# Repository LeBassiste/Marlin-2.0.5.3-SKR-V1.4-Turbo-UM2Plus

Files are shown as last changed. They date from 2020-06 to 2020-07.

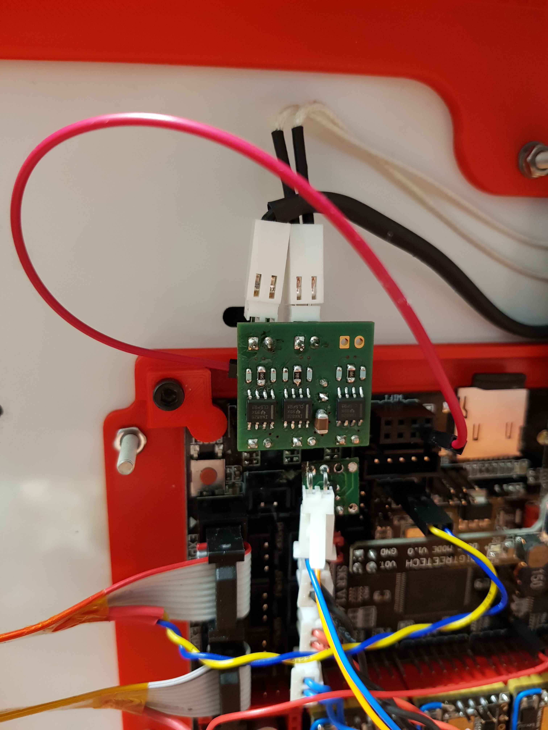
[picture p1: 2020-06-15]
PT100_Amp_Close-up.jpg

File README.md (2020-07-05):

# Marlin-2.0.5.3-SKR-V1.4-Turbo-UM2Plus
Marlin 2.0.5.3 Settings for BIGTREE SKR 1.4_Turbo, TMC5160 to drive Ultimaker UM2+ 3D Printer
version V2 contains updated and sanitized header files to reflect changes in
configuration.h
configuration_adv.h
pins_BT_SKR_c ommon.h
search for "habe" to find all modifications

reduced spill when preloading hotend before print.
increased motor currents to 800 mA and 32 microsteps to improve wall smoothness.

1.Required Hardware					
  a.  1	 BTT SKR 1.4 Turbo				
  b.  4	TMC5160 Stepper drivers				
  c.  1	BTT DCDC Power Module for SKR 1.4				
  d.  1	 PT100 Pre-Amplifier (Ultimaker Style), 3 channel, must use VDD = 3.3 VDC (DIY), see KICAD file	SKR14_PT100_Amp		
  e.  1	MOSFET Adapter Board to run Hotend Fan off of SERVO connector (DIY), see KICAD file SKR14_FAN_DRIVE				

2. What will these Mods do?					
	a.  Enable flicker-free dimmable Case Lighting, using the original Ultimaker Case LEDs @ 24 VDC and high frequency PWM dimming		
	b.  enable PWM-controlled Parts Fan				
	c.  enable PWM-controlled 5VDC for use with Hotend Fan	(needs extra MOSFET and Diode, driven from SERVO connector)			
	d.  increase Bed-Heater and Hotend-Heater PWM to 60 Hz to smoothen power consumption (note: you must use PID for Bed Heater). 
      This improves print quality!				
	e.  enable ulticontroller display and Clickwheel+LEDs as published by Anthrix https://community.ultimaker.com/topic/30786-ultimaker-with-skr-14/

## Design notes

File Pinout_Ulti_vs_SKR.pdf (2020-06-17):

Marlin 2.0.5.3 Settings for BIGTREE SKR 1.4_Turbo, TMC5160 to drive Ultimaker UM2+ 3D Printer

Required Hardware | | this sheet version: | 0.2 | added info about removing R25, R26
1 BTT SKR 1.4 Turbo
4 TMC5160 Stepper drivers
1 BTT DCDC Power Module for SKR 1.4
1 PT100 Pre-Amplifier (Ultimaker Style), 3 channel, must use VDD = 3.3 VDC (DIY)
1 MOSFET Adapter Board to run Hotend Fan off of SERVO connector (DIY)
What will these Mods do?
| Enable flicker-free dimmable Case Lighting, using the original Ultimaker Case LED-Strips
| enable PWM-controlled Parts Fan
| enable PWM-controlled 5VDC for use with Hotend Fan
| increase Bed-Heater and Hotend-Heater PWM to 60 Hz to smoothen power consumption (note: you must use PID for Bed Heater). This improves print quality.
| enable ulticontroller display and Clickwheel+LEDs (as published by Anthrix here:…) | https://community.ultimaker.com/topic/30786-ultimaker-with-skr-14/
Item | Spec1 | Spec2 | Spec3 | Ultimainboard | SKR 1.4 Port | SKR 1.4 | SKR-Spec1 | !!! Required HW Changes !!! | where?
Bed-Heater | 24VDC | SW-PWM | Screw Term | J21:1-2 / Heated-Bed | P_205 | HB | | | File | line
Bed-Temp | PT100 | MOLEX 2 | J13 / Temp3 | P_025 | TB | JJ12

must use Ultimaker-Style PT100 Pre-Amp
| | | | | | | must remove R26 on SKR board | configuration.h | 415 | #define TEMP_SENSOR_BED 20
Case Light | 24VDC | HF-PWM | MOLEX 2 | J15 | P_203 | FAN0 | Configuration_adv-h | 431 | #define CASE_LIGHT_PIN P2_03
E-Stepper | | | J30 | | E0M
Hotend-Fan | 5VDC | PWM | J34 | P_200 | SERVOS | J22:1_SIG, :2_NPWR, :3_GND | must use BTT DC/DC Extender and extra MOSFET | Configuration_adv-h | 423 | #define E0_AUTO_FAN_PIN P2_00
Hotend-Heater | 24VDC | SW-PWM | J21:5-6 / Heater 1 | P_207 | HE0
Hotend-Temp | PT100 | MOLEX 2 | J7 | P_024 | TH0 | J11
Part Fan | 24VDC | PWM | J14 | P_204 | HE1 | must use Ultimaker-Style PT100 Pre-Amp must remove R25 on SKR board | configuration.h | 409 | #define TEMP_SENSOR_0 20
| | | | | | | pins_BTT_SKR_common.h | 66 | #define FAN1_PIN P2_04
| | | | | | | | 86 | #define FAN_PIN P2_04
X-Stepper | J27
X-Stop | | J5 | P_129 | X-Stop | J1:1_P5, :2_GND, :3_SIG | connect to :2_GND, :3_SIG, pull to GND on activate
Y-Stepper | | J28
Y-Stop | | J8 | P_128 | Y-Stop | J3 | connect to :2_GND, :3_SIG, pull to GND on activate
Z-Stepper | | J29
Z-Stop | | J6 | P_127 | Z-Stop | J4 | connect to :2_GND, :3_SIG, pull to GND on activate
Ulticontroller E1 | 2Mx5_0.100 | J32 | | E1DET | | Anthrix mod (I2C and 3.3V supply) | configuration.h | 1933 | #define ULTI_CONTROLLER
Ulticontroller E2 | 2Mx5_0.101 | J33 | | E0DET | | Anthrix mod (I2C and 3.3V supply)
PWM frequency for Case Light, Fans_1 | P_124 uses 60 Hz PWM, not useful for lighting | HW-PWM frequeny default is too high, use frequency definition | must use free-wheeling diodes on outputs | Configuration_adv-h | 384 | #define FAST_PWM_FAN_FREQUENCY 31400
PWM frequency for Case Light, Fans_2 | | | | | | | must use free-wheeling diodes on outputs | configuration.h | 2089 | #define FAST_PWM_FAN
Power smoothing on 24VDC | standard SW PWM causes too much ripple | | | new frequency approx. 60 Hz. reduced resolution, but that's ok for heaters | | | | configuration.h | 2101 | #define SOFT_PWM_SCALE 3
Ulticontroller Color Wheel | | | | | | | | configuration.h | 2124 | #define PCA9632

Marlin 2.05

#include "../lpc1768/pins_BTT_SKR_V1_4.h" #include "pins_BTT_SKR_common.h"

Connector | Connect what:

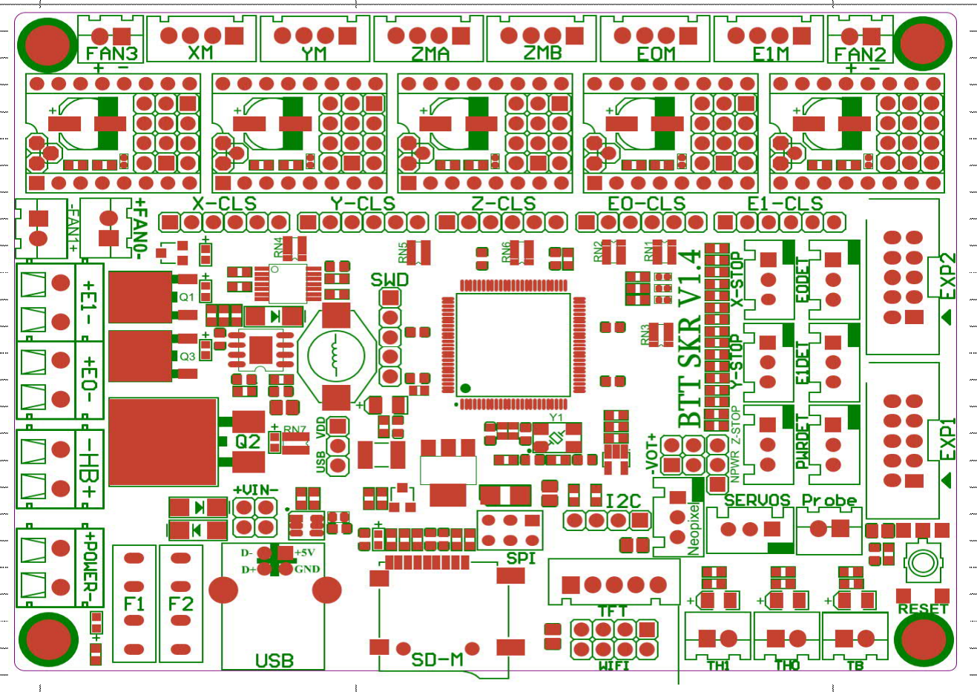
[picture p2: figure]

FAN0: | CASE LIGHT (24 VDC) | Connector | Connect what:
E1: | PARTS FAN (24 VDC) | EXP1 | Ulticontroller w/ modded cable
E0: | HOTEND | EXP2 | Ulticontroller w/ modded cable
HB: | HEATER-BED
Connector | Connect what:
TH0 | PT100 Pre-Amp, Hotend
TB | PT100 Pre-Amp, Heater-Bed
SERVO | HOTEND-FAN (5 VDC), via MOSFET Adapter Board

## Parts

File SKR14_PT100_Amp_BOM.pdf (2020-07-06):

PROJECT: | ...\KICAD\SKR14_PT100_Amp\SKR14_PT100_Amp.pro
Version: | 1.0 | sanitized digikey entries
ref | value5 | footprint | Digikey | Price | comment
C1 | 100nF | Capacitor_SMD:C_0603_1608Metric | 399-1100-1-ND | 0,09 €
C10 | 100nF | Capacitor_SMD:C_0603_1608Metric | 399-1100-1-ND | 0,09 €
C11 | 100nF | Capacitor_SMD:C_0603_1608Metric | 399-1100-1-ND | 0,09 €
C12 | 100nF | Capacitor_SMD:C_0603_1608Metric | 399-1100-1-ND | 0,09 €
C13 | dnp | Capacitor_SMD:C_0603_1608Metric | - | € do not populate
C14 | dnp | Capacitor_SMD:C_0603_1608Metric | - | € do not populate
C15 | dnp | Capacitor_SMD:C_0603_1608Metric | - | € do not populate
C16 | 10uF / 25V | Capacitor_SMD:C_0805_2012Metric_Pad1.15x1.40mm_HandSolder | 490-10503-1-ND | 0,34 €
C2 | 100nF | Capacitor_SMD:C_0603_1608Metric | 399-1100-1-ND | 0,09 €
C3 | 100nF | Capacitor_SMD:C_0603_1608Metric | 399-1100-1-ND | 0,09 €
C4 | 100nF | Capacitor_SMD:C_0603_1608Metric | 399-1100-1-ND | 0,09 €
C5 | 100nF | Capacitor_SMD:C_0603_1608Metric | 399-1100-1-ND | 0,09 €
C6 | 100nF | Capacitor_SMD:C_0603_1608Metric | 399-1100-1-ND | 0,09 €
C7 | 100nF | Capacitor_SMD:C_0603_1608Metric | 399-1100-1-ND | 0,09 €
C8 | 100nF | Capacitor_SMD:C_0603_1608Metric | 399-1100-1-ND | 0,09 €
C9 | 100nF | Capacitor_SMD:C_0603_1608Metric | 399-1100-1-ND | 0,09 €
J1 | Conn_01x02_Male Connector_Molex:Molex_KK-254_AE-6410-02A_1x02_P2.54mm_Vertical | WM13445-ND | 0,44 €
J2 | Conn_01x02_Male Connector_Molex:Molex_KK-254_AE-6410-02A_1x02_P2.54mm_Vertical | WM13445-ND | 0,44 €
J3 | Conn_01x02_Male Connector_Molex:Molex_KK-254_AE-6410-02A_1x02_P2.54mm_Vertical | WM13445-ND | 0,44 €
J4 | Conn_01x02_Male Connector_PinHeader_2.54mm:PinHeader_1x02_P2.54mm_Vertical | 609-6263-ND | 0,09 € bottom side
J5 | Conn_01x02_Male Connector_PinHeader_2.54mm:PinHeader_1x02_P2.54mm_Vertical | SAM1011-02-ND | 0,42 € use female connector, bottom side
J6 | Conn_01x02_Male Connector_PinHeader_2.54mm:PinHeader_1x02_P2.54mm_Vertical | SAM1011-02-ND | 0,42 € use female connector, bottom side
J7 | Conn_01x02_Male Connector_PinHeader_2.54mm:PinHeader_1x02_P2.54mm_Vertical | SAM1011-02-ND | 0,42 € use female connector, bottom side
R1 | 2k2 | Resistor_SMD:R_1206_3216Metric | YAG5058CT-ND | 0,35 €
R10 | 10k | Resistor_SMD:R_0603_1608Metric | 541-2795-1-ND | 0,13 €
R11 | 10k | Resistor_SMD:R_0603_1608Metric | 541-2795-1-ND | 0,13 €
R12 | 10k | Resistor_SMD:R_0603_1608Metric | 541-2795-1-ND | 0,13 €
R13 | 5k49 | Resistor_SMD:R_0805_2012Metric_Pad1.15x1.40mm_HandSolder | A140485CT-ND | 0,57 €
R14 | 5k49 | Resistor_SMD:R_0805_2012Metric_Pad1.15x1.40mm_HandSolder | A140485CT-ND | 0,57 €
R15 | 5k49 | Resistor_SMD:R_0805_2012Metric_Pad1.15x1.40mm_HandSolder | A140485CT-ND | 0,57 €
R16 | 100 | Resistor_SMD:R_0603_1608Metric | 541-2976-1-ND | 0,12 €
R17 | 100 | Resistor_SMD:R_0603_1608Metric | 541-2976-1-ND | 0,12 €
R18 | 100 | Resistor_SMD:R_0603_1608Metric | 541-2976-1-ND | 0,12 €
R19 | 100 | Resistor_SMD:R_0603_1608Metric | 541-2976-1-ND | 0,12 €
R2 | 2k2 | Resistor_SMD:R_1206_3216Metric | YAG5058CT-ND | 0,35 €
R20 | 100 | Resistor_SMD:R_0603_1608Metric | 541-2976-1-ND | 0,12 €
R21 | 100 | Resistor_SMD:R_0603_1608Metric | 541-2976-1-ND | 0,12 €
R3 | 2k2 | Resistor_SMD:R_1206_3216Metric | YAG5058CT-ND | 0,35 €
R4 | 2k2 | Resistor_SMD:R_1206_3216Metric | YAG5058CT-ND | 0,35 €
R5 | 2k2 | Resistor_SMD:R_1206_3216Metric | YAG5058CT-ND | 0,35 €
R6 | 2k2 | Resistor_SMD:R_1206_3216Metric | YAG5058CT-ND | 0,35 €
R7 | 10k | Resistor_SMD:R_0603_1608Metric | 541-2795-1-ND | 0,13 €
R8 | 10k | Resistor_SMD:R_0603_1608Metric | 541-2795-1-ND | 0,13 €
R9 | 10k | Resistor_SMD:R_0603_1608Metric | 541-2795-1-ND | 0,13 €
U1 | INA826 | Package_SO:SOIC-8_3.9x4.9mm_P1.27mm | 296-30238-1-ND | 2,42 €
U2 | INA826 | Package_SO:SOIC-8_3.9x4.9mm_P1.27mm | 296-30238-1-ND | 2,42 €
U3 | INA826 | Package_SO:SOIC-8_3.9x4.9mm_P1.27mm | 296-30238-1-ND | 2,42 €
| | | Sum ex VAT | 16,67 €
| | | VAT 19% | 3,17 €
Total | 19,84 €

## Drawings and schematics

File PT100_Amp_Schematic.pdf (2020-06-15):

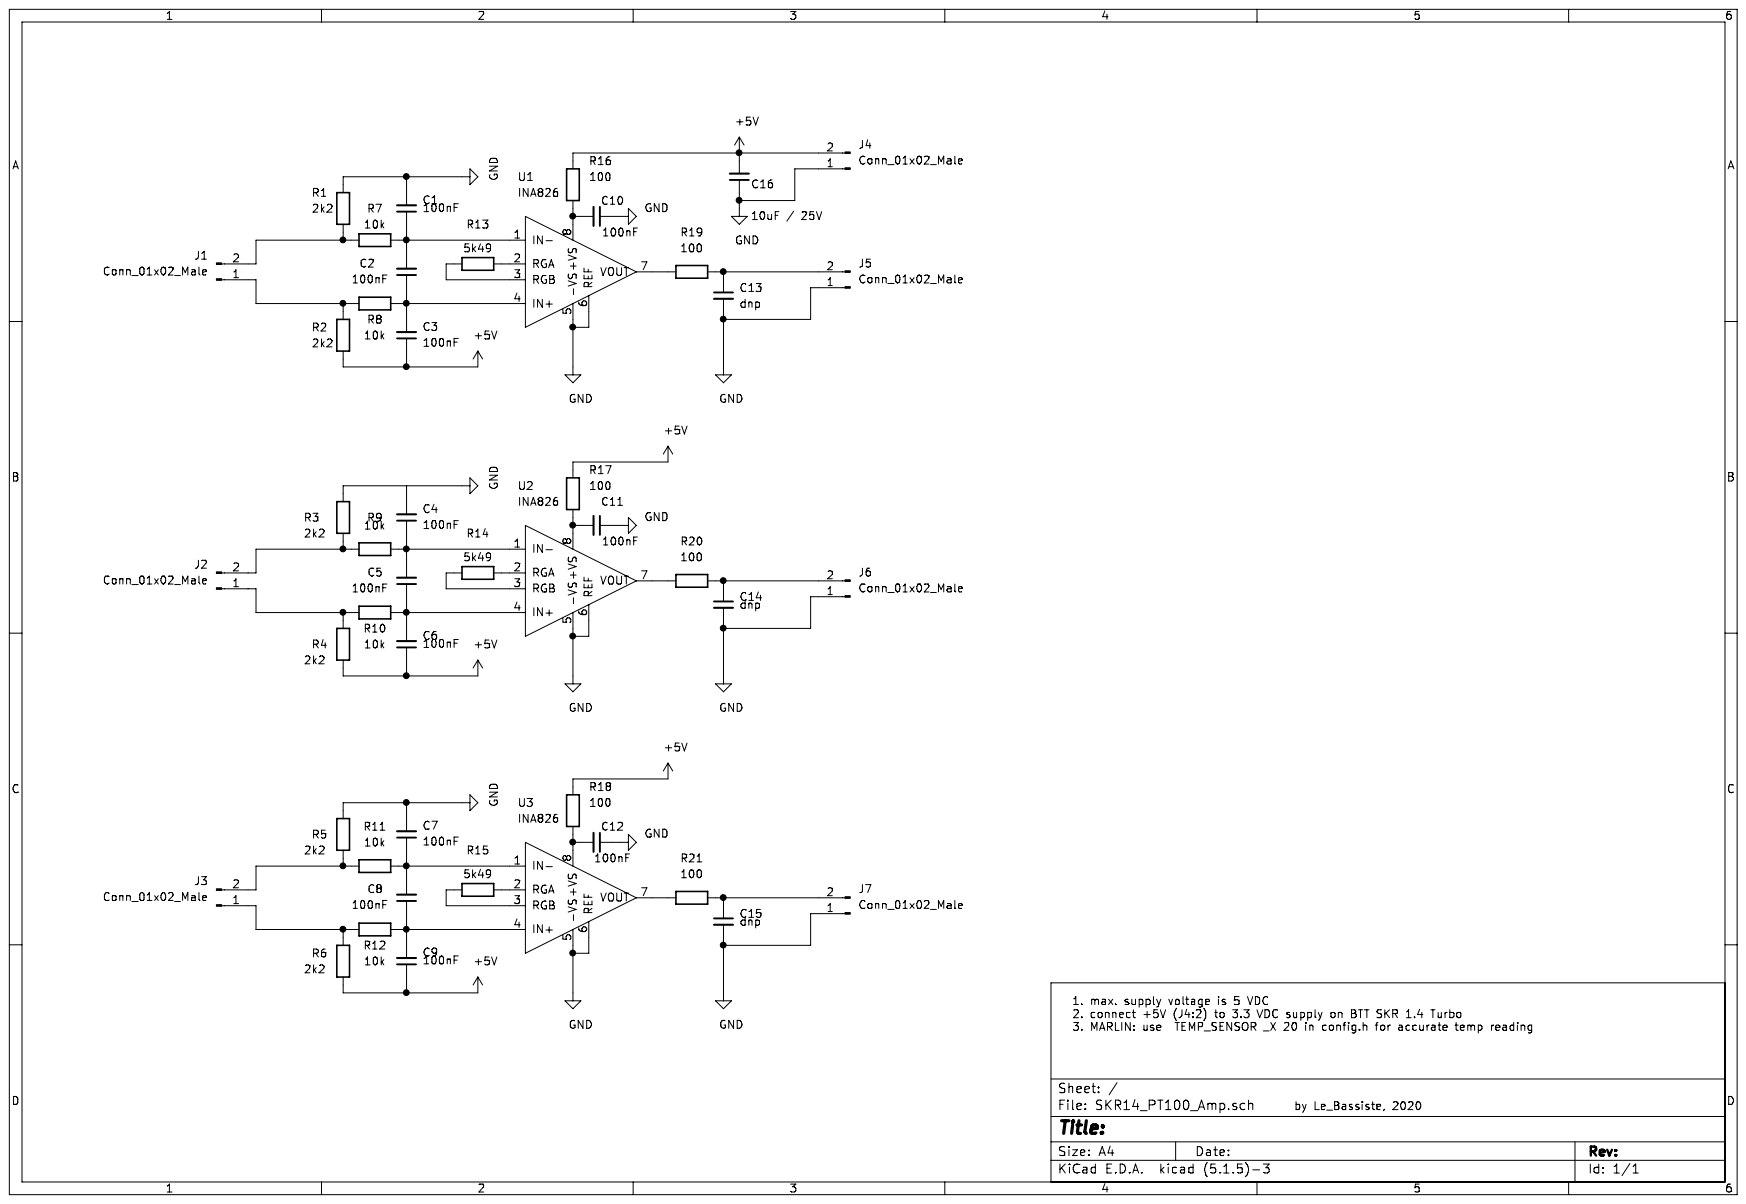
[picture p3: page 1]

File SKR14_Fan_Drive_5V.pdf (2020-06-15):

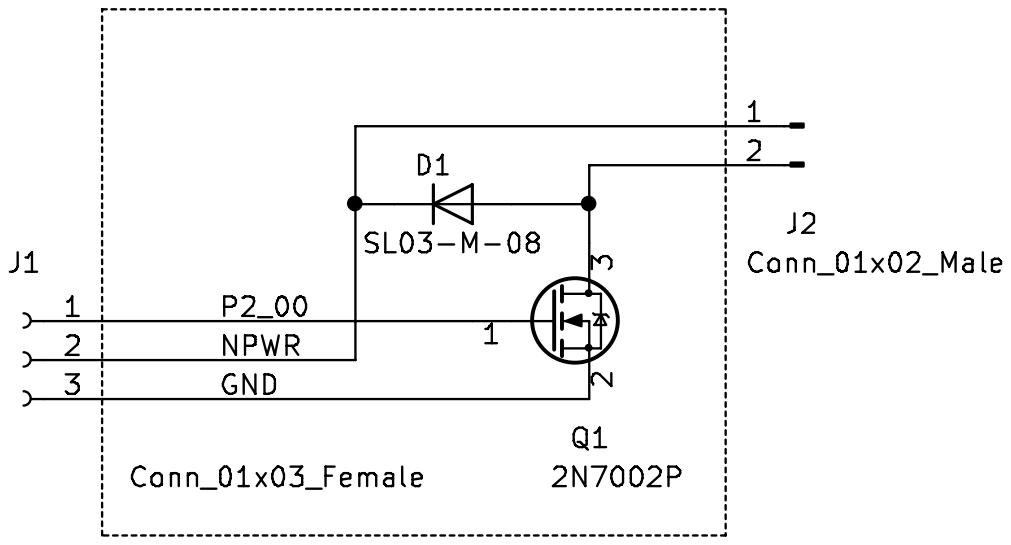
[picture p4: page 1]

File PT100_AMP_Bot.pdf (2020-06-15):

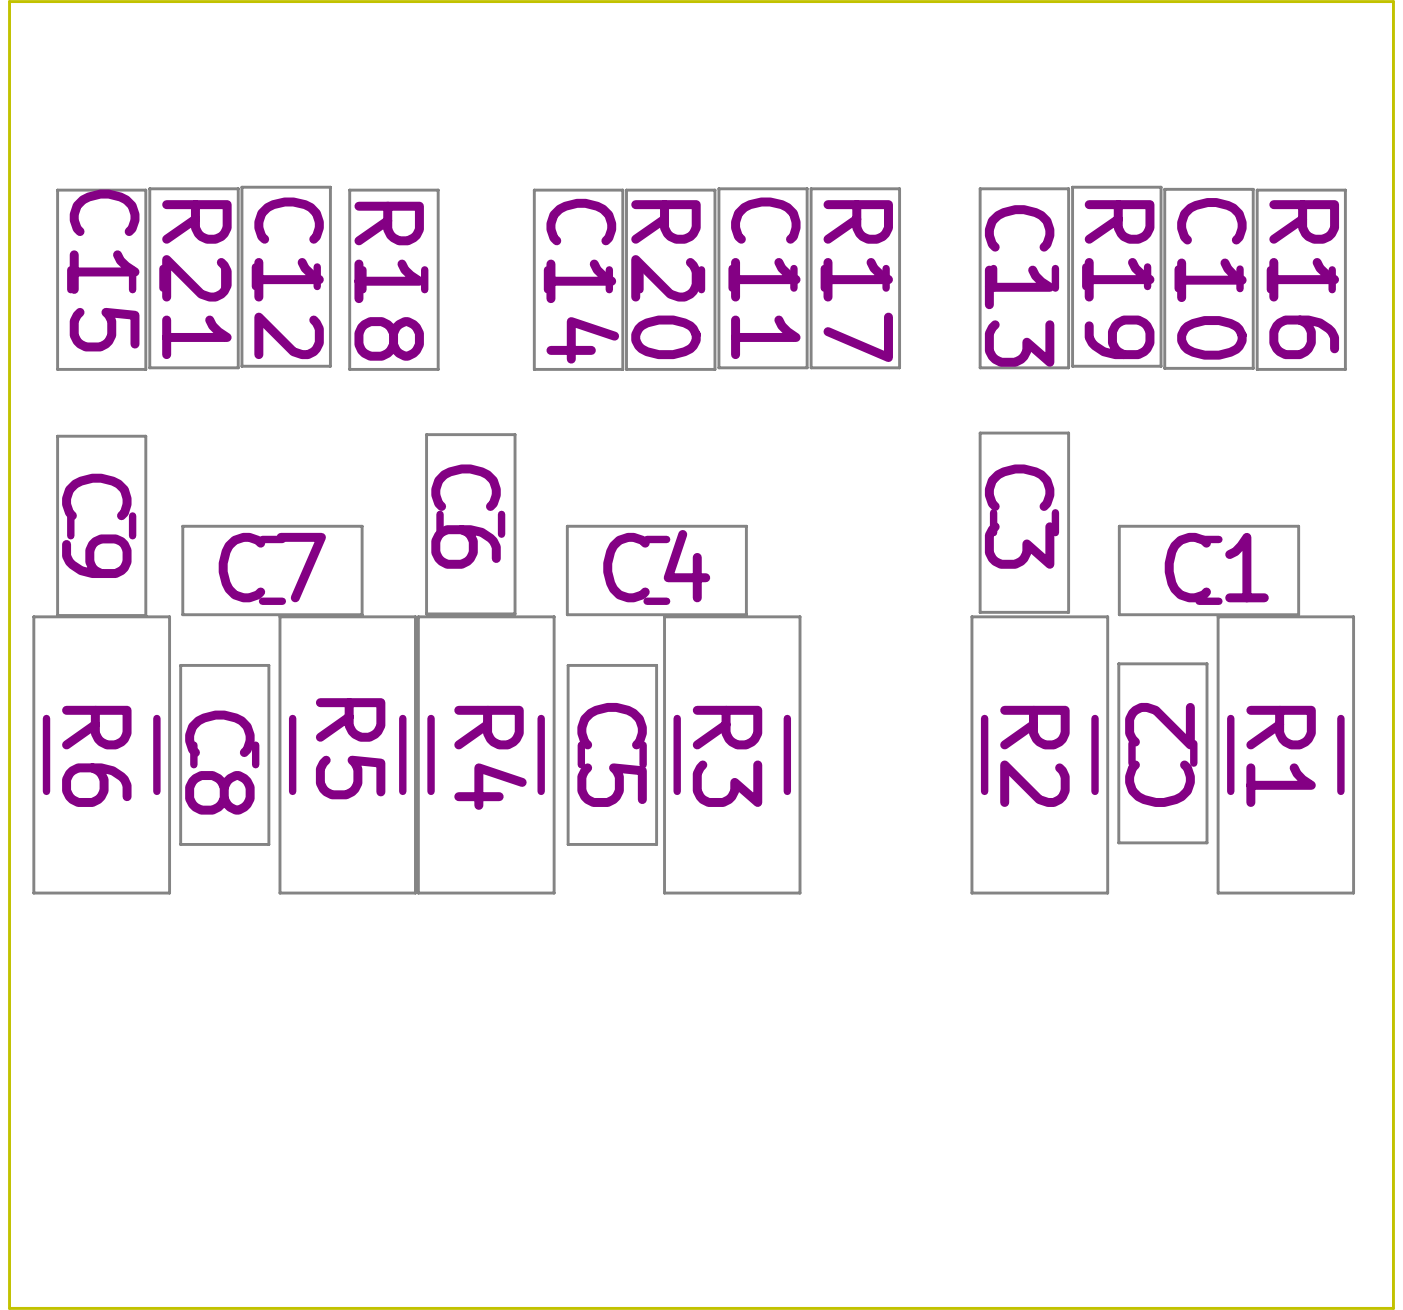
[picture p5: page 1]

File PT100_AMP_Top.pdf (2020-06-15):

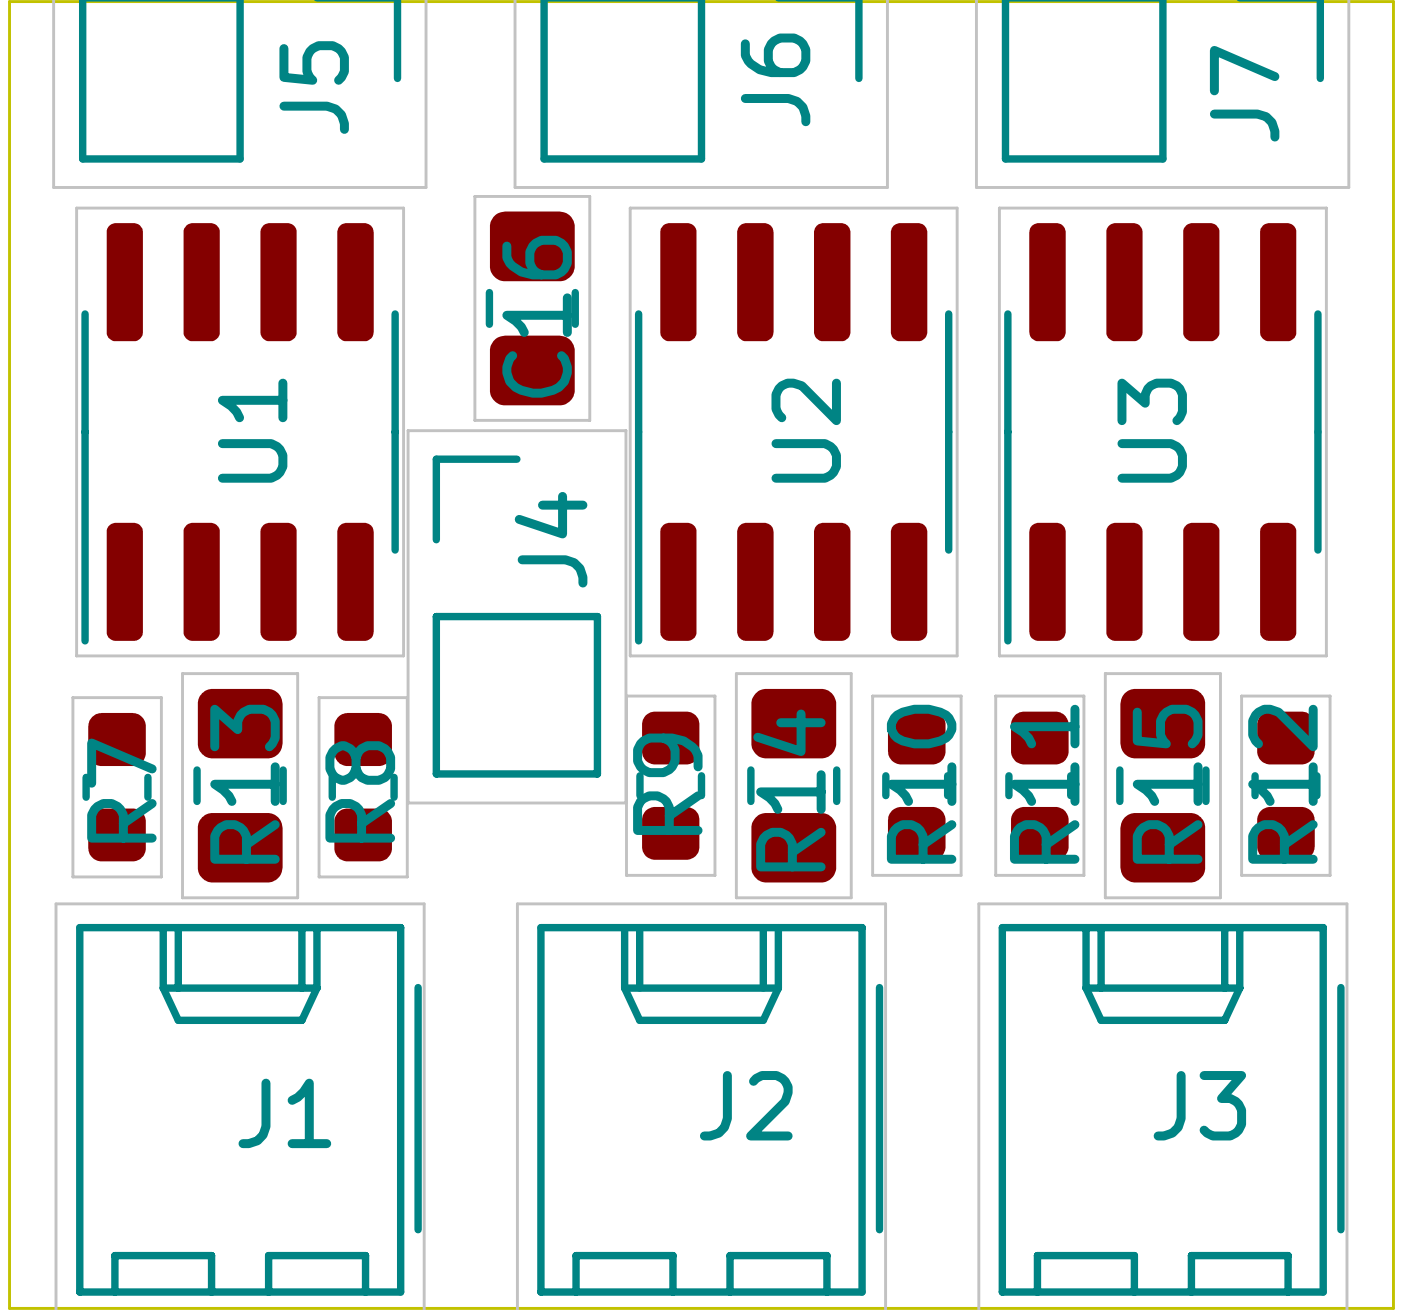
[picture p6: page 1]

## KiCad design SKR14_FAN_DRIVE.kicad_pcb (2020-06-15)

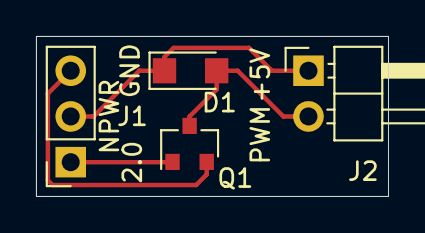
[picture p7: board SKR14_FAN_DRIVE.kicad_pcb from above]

Board: 2 copper layers, 19.6 x 8.9 mm, 4 parts (0 on the bottom side), 4 nets.

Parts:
D1: SL03-M-08; D_SMF
J1: Conn_01x03_Female; PinSocket_1x03_P2.54mm_Vertical
J2: Conn_01x02_Male; PinHeader_1x02_P2.54mm_Horizontal
Q1: 2N7002P; SOT-23

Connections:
/GND: J1.3, Q1.2
/NPWR: D1.1, J1.2, J2.1
/P2_00: J1.1, Q1.1
unnamed: D1.2, J2.2, Q1.3

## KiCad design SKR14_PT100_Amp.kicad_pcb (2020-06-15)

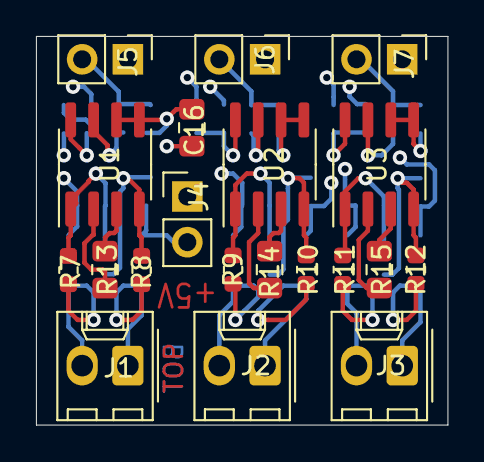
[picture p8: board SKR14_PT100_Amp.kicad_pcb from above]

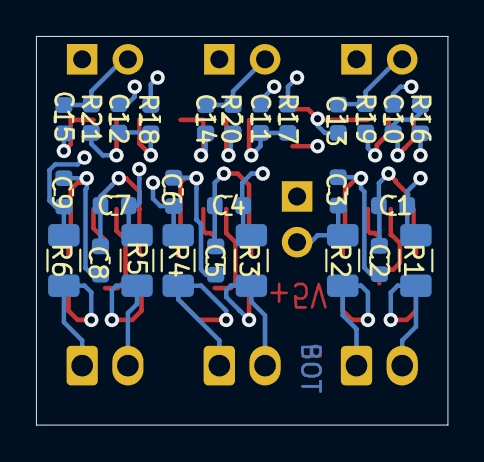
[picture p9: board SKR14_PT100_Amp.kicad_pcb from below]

Board: 4 copper layers, 22.9 x 21.6 mm, 47 parts (27 on the bottom side), 29 nets.

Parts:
C1, C2, C3, C4, C5, C6, C7, C8, C9, C10, C11, C12: 100nF; C_0603_1608Metric
C13, C14, C15: dnp; C_0603_1608Metric
C16: 10uF / 25V; C_0805_2012Metric_Pad1.15x1.40mm_HandSolder
J1, J2, J3: Conn_01x02_Male; Molex_KK-254_AE-6410-02A_1x02_P2.54mm_Vertical
J4, J5, J6, J7: Conn_01x02_Male; PinHeader_1x02_P2.54mm_Vertical
R1, R2, R3, R4, R5, R6: 2k2; R_1206_3216Metric
R7, R8, R9, R10, R11, R12: 10k; R_0603_1608Metric
R13, R14, R15: 5k49; R_0805_2012Metric_Pad1.15x1.40mm_HandSolder
R16, R17, R18, R19, R20, R21: 100; R_0603_1608Metric
U1, U2, U3: INA826; SOIC-8_3.9x4.9mm_P1.27mm

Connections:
+5V: C3.1, C6.1, C9.1, C16.2, J4.2, R2.2, R4.2, R6.2, R16.1, R17.1, R18.1
GND: C1.2, C4.2, C7.2, C10.1, C11.1, C12.1, C13.2, C14.2, C15.2, C16.1, J4.1, J5.1, J6.1, J7.1, R1.1, R3.1, R5.1, U1.5, U1.6, U2.5, U2.6, U3.5, U3.6
unnamed: C1.1, C2.2, R7.1, U1.1
unnamed: C2.1, C3.2, R8.1, U1.4
unnamed: C4.1, C5.2, R9.1, U2.1
unnamed: C5.1, C6.2, R10.1, U2.4
unnamed: C7.1, C8.2, R11.1, U3.1
unnamed: C8.1, C9.2, R12.1, U3.4
unnamed: C10.2, R16.2, U1.8
unnamed: C11.2, R17.2, U2.8
unnamed: C12.2, R18.2, U3.8
unnamed: C13.1, J5.2, R19.1
unnamed: C14.1, J6.2, R20.1
unnamed: C15.1, J7.2, R21.1
unnamed: J1.1, R2.1, R8.2
unnamed: J1.2, R1.2, R7.2
unnamed: J2.1, R4.1, R10.2
unnamed: J2.2, R3.2, R9.2
unnamed: J3.1, R6.1, R12.2
unnamed: J3.2, R5.2, R11.2
unnamed: R13.1, U1.2
unnamed: R13.2, U1.3
unnamed: R14.1, U2.2
unnamed: R14.2, U2.3
unnamed: R15.1, U3.2
unnamed: R15.2, U3.3
unnamed: R19.2, U1.7
unnamed: R20.2, U2.7
unnamed: R21.2, U3.7

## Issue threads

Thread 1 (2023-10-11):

FW change instead of HW for the PT100

totoantibes, 2023-10-11:
As i am looking to swap my ultimaker 2.14 board i a have more of a question than an Issue:
instead of replicating the ultimaker preamp circuit for the PT100 is it not possible to play with the  configuration.h thermal settings with

`#define TEMP_SENSOR_0  -5 //: MAX31865 with Pt100/Pt1000, 2, 3, or 4-wire  (only for sensors 0-1)
// Resistor values when using MAX31865 sensors (-5) on TEMP_SENSOR_0 / 1
#if TEMP_SENSOR_IS_MAX_TC(0)
  #define MAX31865_SENSOR_OHMS_0      100 // (Ω) Typically 100 or 1000 (PT100 or PT1000)
  #define MAX31865_CALIBRATION_OHMS_0 430 // (Ω) Typically 430 for Adafruit PT100; 4300 for Adafruit PT1000
#endif`

thanks

LeBassiste, 2023-10-12:
you didn't mention what new board exactly you are planning to use instead of the original ultimaker 2.14 board.  if the new board has a MAX31865, then the above configuration may work. if the new board does not have the MAX31865, then it will defo not work.  note that the MAX31865 is an external ADC that interfaces to the board's processor via I2C (or TWI for that matter), whereas:
1. the original ultimaker board uses the internal ADC of its processor to read amplified temp values from the printer's PT100 sensor and has the required pramplifier built in.
2. if you are planning to use a board that was originally intended to be used with NTC sensors (as opposed to PT100 sensors) on its internal ADC, the you must use a preamplifier.

totoantibes, 2023-10-12:
Thanks for the details. I am planning on using the SKR 1.4 turbo board.

totoantibes, 2023-10-12:
> @totoantibes, I've converted my Ultimaker 2 to an SKR 1.4 Turbo board a few years ago. Feel free to check out my repository, it might be useful to you.

Thanks. does look in line with my plans. Will continue questions on your repo then

Closed 2023-10-12.

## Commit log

2020-07-05 Delete Marlin-2.0.5.3-SKR1.4T_UM2plus.zip
    deleted for version V2 with sanitized header files. search for "habe" to find all changes.
2020-07-06 Add files via upload
    BOM for PT100_Amp, including Digikey order numbers.
